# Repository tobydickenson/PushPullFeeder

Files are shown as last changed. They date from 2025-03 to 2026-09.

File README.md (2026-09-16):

# PushPullFeeder

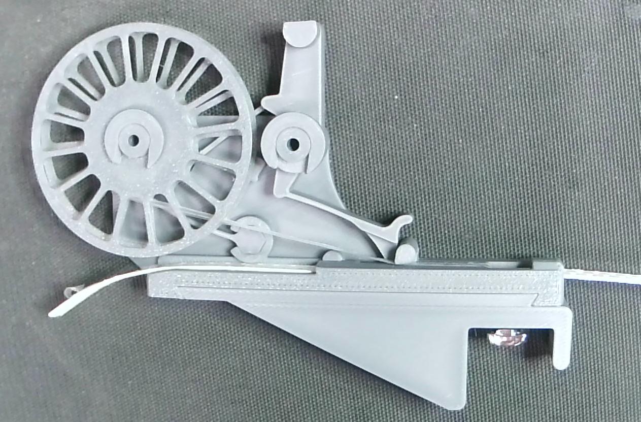
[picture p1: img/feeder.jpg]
A PushPull Feeder


This is a fork of Markmaker’s awesome [PushPullFeeder](https://github.com/markmaker/PushPullFeeder). All of the genius in this design should be credited to Mark, and Mark's [blog](https://makr.zone/?p=399) is a great introduction. Here I present some refinements:

- Some general usability and maintainability improvements.
- A new Bumper Cam mechanism for engaging and disengaging the pushing mechanism with the sprocket hole which greatly improves smoothness.
- Some incremental improvements for feeding parts which were already handled well in Mark’s baseline design.
- Some new features for feeding parts which were outside the scope of Mark’s original design: Parts with deep wide embossed pockets; from 8mm tape with 4mm pockets, up to 24mm with 11mm pockets tested to be working well.
- An alternative machine mounting scheme which is particularly suitable for the lumenpnp machine. This model still supports Mark's mounting scheme too.

The original model supports a dazzling array of configuration parameters. Here I present some useful parameter sets that I use in production on the lumenpnp.

# Changes in Release 176 (March 2026)

- Printability improvements for Bambu printers - My main printer is now A1 mini.
- A huge increase in smoothness. Previous versions push the tape with a pair of sprung teeth. In previous versions a tooth on the pusher dog drags along the top surface of the tape then drops into a sprocket hole before pushing forward. The tape is then pushed over the reverse-blocking tooth, which pops into the sprocket hole at the end of the push. All of these actions cause vibrations and impacts on the tape surface which can cause vibrations which jump 0603 and smaller parts out of pockets. This version uses "the bumper" cam which actively lifts the tooth out of one sprocket hole, and lowers into the next before pushing forward. The reverse-blocking tooth is removed entirely. Having eliminated the main causes of vibrations, it has been possible to eliminate some other vibration-mitigation features which further improves the smoothness of the feed.
- The lever part is much more robust. This is due to some design refinements and some changes to the printing recommendations.
- A compliant spring mechanism to gently support the underside of the tape and hold its top surface at the correct Z position.
- An improved friction clutch for film peeling.
- Further improvement to prevent the tape getting jammed. A jammed tape can cause the lever to break when activated.
- Improved rigidity on the machine mount.
- Some changes to recommended printer settings - see below.
- Change to assist in assembling the film peeling spool onto the base.

## Changes since the first alpha release of this branch

- Increased peeling force.
- Changes to the compliant spring and base to accomodate super-thin and super-fat tapes.
- Move the paper tape pick window for better alignment with 0402 parts.
- Fix a chamfer on the lever axle hole.
- Change some through holes to blind holes for a cleaner faster bottom surface print.

# Changes in Release 74 (August 2025) excluding those later reverted in Release 176

## Improvements for parts in paper tape
- The "inset" is the part which holds the tape as it passes through the feeder. There are several changes to the profile of the inset to reduce part jumpiness.
- The grip after the pick window is arched to allow any mispicked parts to be expelled out the front of the feeder.
- A gentle lead-in to help insert the tape into the back of the inset.

## Improvements for parts in embossed plastic tape
- An option to print the inset in two halves. The left half supports under the sprocket holes on the left side of the tap. The right half supports under the right side of the tape, and grips the tape from above. This avoids any geometry limitations due to 3d printer overhang angle, and allows insets for tapes with deep and wide embossed pockets.

## Improvements for cover film peeling
- The film peeling edge has been remodelled to ensure it is perpendicular to the tape feed direction, which reduces the risk of the film tearing.
- A narrower mount for the peeling spring gives a clearer path for film onto the peeling spool.
- With wider tapes, the friction wheel sometimes had a problem where there is an excess of friction due to a large contact area, and the peeling force is too large. The film can pull the tape ahead of the sprocket hole engagement. A tapered friction wheel controls the contact area used with wider tapes.
- “The scraper” is a new optional feature which can be used for feeding parts that tend to stick to the film rather than stay in their pocket. This is a finger which holds the parts in their pocket until they advace to the pick location.

## Changes to the lever
- Mark's original design horizontally scaled the lever and various other design features in proportion to the tape width. That scheme has been changed to have a fixed width lever. I think this makes more sense; tapes of all widths are advanced using sprocket holes of the same dimensions. Furthermore this reduces the number of different parts that need to printed.
- There are some geometry changes to give more space around any part that might be carried by the other nozzle on a dual-nozzle machine. Firstly, the angle of the lever arm has been changed to be exactly vertical. This increases the X/Y space available for the part on the other nozzle.
- Secondly, the knob at the top of the lever arm has a flatter profile. This increases the Z space available for the part on the other nozzle.

## Usability and printability improvements
- Added some fillets in places which previously saw some brittle fractures.
- Sometimes the inset can be a tight fit on the base, so some features have been added to aid disassembly. Finger grips for pulling it off, and a second hole through the base for pushing it off.
- Improved retention of the film peeler spool washer, or reel-holder arm counterpart.

## A new optional machine mount.
Use with the lumenpnp has several design requirements that are quite different to Mark’s baseline design.

- The lumenpnp head has a large Y offset between nozzles and camera which makes it impractical to use the camera with the PushPull feeder. Since we can’t use the camera to fine-tune the pick location, we benefit from the pick location being very stable and repeatable. The feeder is therefore mounted onto a 20mm extrusion directly underneath the pick location. This new 20mm extrusion is mounted to the machine side rails using 2 angle brackets at each end for rigidity. See photos below.
- The feeder is mounted onto the extrusion using a 6mm M3 countersunk screw and t-nut, directly underneath the pick location. The screw is captive in the feeder once the inset is fitted, and the screw can be driven through a hole in the base of the inset so that it can be fitted and removed while tape is loaded on the feeder; you just need to cut off the empty tape end, and retract the tape a little to expose the hole.
- There is a separate git repository for a [lumenpnp z gantry](https://github.com/tobydickenson/PushPullGantry) modification which includes the hook needed for pushing and pulling the feeder lever.

## Extra-deep feeders
- This includes a configuration for a feeder for parts up to 11mm tall in 16mm or 24mm tape. This feeder has a deeper base and deeper inset to support the deep tape.
- A correspondingly shorter lever is used to maintain a safe-z height consistent with the normal feeders. This needs a slightly slower push/pull speed.

# How to print

STL files for immediate printing are in the `printme` directory.

All parts should be printed in PETG. PETG has a stable modulus over temperature, which is required for the spring parts. PETG has good abrasion resistance, which is required for the lever and base which interact at "the bumper".

All models are tested on a Bambu printer with 0.4mm nozzle. All parts print with the standard "0.12mm High Quality" print profile, with the exception of the Lever part (see below)

For other slicers, use a "layer start: sharpest corner" or "seam: aligned" option. Plain bearing surfaces have a helical groove which is designed to capture the layer start, ensuring that the exposed bearing surface is a smooth continous extrusion.

IMPORTANT: Before printing, it is critical that your printer can produce dimensionally accurate parts. Print the `printme/nuts/nuts-xxx.stl` file, and perform the following checks:

- Check the bottom surface (first layer) is smooth and correct. A textured build plate is ok.
- Check the top surface is smooth and correct. It is ok to have some under-extrusion visible in the top surface, and indeed this is better than a precise flow calibration which shows a smooth top surface but makes surface dimensions more sensitive to any variation in flow.
- Check the parts are circular, not elliptical.
- Check the parts are circular, not a lower polygon count approximation substituted by your slicer.
- Check the outer diameter of the male part is 8.00mm, and its surface is smooth. This is a dimension accuracy check.
- Check the inner diameter of the female part printed with "10" is 8.10mm. This is labelled 10 because of the 10x10µm size increase. Fitting the male part inside this hole is a validation check of axle plain bearings. The axle should turn smoothly, without being loose. See the assembly video (linked below) for how this axle should appear.
- Check the inner diameter of the other female part printed with "0" is 8.00mm. Fitting the male part inside this hole is a validation of interference fit assembly.

Any problems need to be addressed first, through either printer hardware maintenance or slicer configuration. The printed feeder is very sensitive to dimensional tolerance; if your printer can't produce an accurate nut then it will not be able to print a working feeder!

If any of the diameters are wrong then you will need to adjust a "X-Y hole compensation" slicer option with a correction offset. Re-print the test nuts and re-check.

The **Lever** parts has a leaf spring feature which needs a modified slicer profile. The important constraint is that the leaf springs must be printed as continuous extrusions; any discontinuities will result in a stress concentration which will make the spring insufficiently robust. On a Bambu printer with 0.4mm nozzle this can be acheived by setting the "Outer wall" and "Inner wall" options to **0.3mm**. Please confirm this has the desired effect using your slicer preview. The leaf springs should be printed as four wall extrusions with no discontinuities, as highlighted in green below. The red highlights show various discontinuities which would cause the leaf spring to be insufficiently robust (although they will still probably feed several thousand parts before breaking with fatigue, so dont panic if this is difficult to get right on your first print).

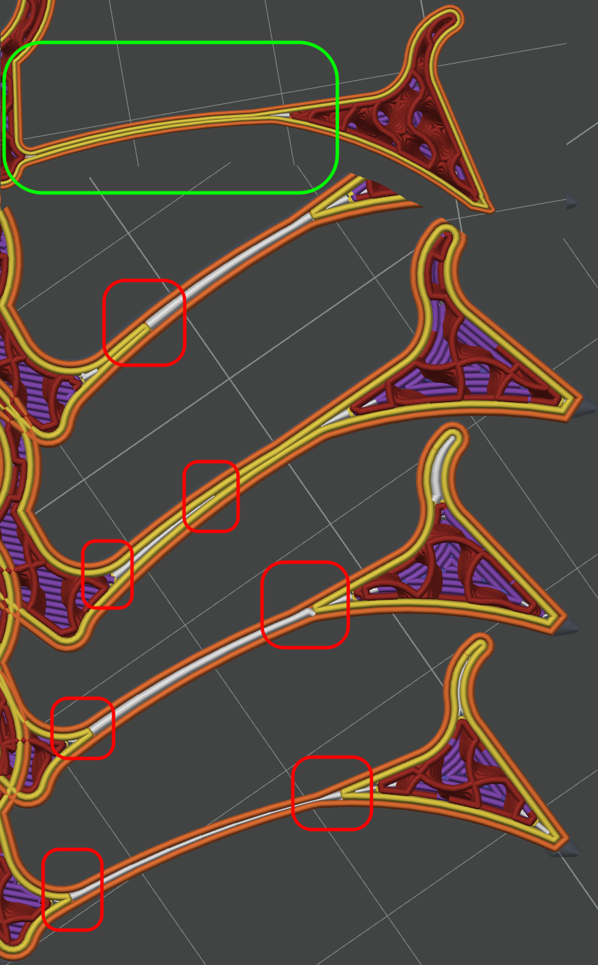
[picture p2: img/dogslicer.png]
Lever slicing


# Recommended movement steps

The movement steps described below are a little different to those described in Mark’s setup video. The key difference is that the start location is in front of the feeder, not above. This means that the programmed push/pull motion takes the hook actuator well away from the feeder, and therefore the push/pull mechanism does not need to be considered when configuring safe-z.

Manually move the feeder’s push/lull lever back to its home position, with the “dog” pusher fully forward against the end stop.

- Set the **Start** location with the tip of the the hook 1mm above the lever, and 10mm in front.
- **Mid1** location should be set with the hook 1mm above the lever, and aligned ready to move down. Note that the “heel” of the hook ensures that the lever is returned back into its home position during the movement to this location.
- **Mid2** location: The hook moves down 3mm and forward 0.5mm. This engages the hook onto the lever.
- **Mid3** location: This is the position with the hook under tension pulling back, pushing the tape forward. Set this position to the same Z as Mid2, and 1.5mm back. You may need to adjust the 1.5mm offset; it needs to push the tape all the way forwards (for repeatable positioning) without unduly bending the lever arm. Set 20ms pause time to ensure the actuator remains momentarily stationary at this end point.
- **End** location: This is the position with the hook under tension pushing forward. Relative to Mid 2 this is 10mm forward and 2.5mm down. 10mm is a good starting point, but you might find this needs to be increased up to around 12mm, depending on machine rigidity. Set 20ms pause time to allow the dog to drop of the top of the bumper cam.

The tickboxes control which locations are visited for the forward and backward stroke, and which locations are repeated when pumping multiple cycles in one visit. As shown below, Mid3 is skipped on the forward cycle, Mid 2 skipped on the backwards cycle, and only Mid3 and End are repeated for multiple cycles.

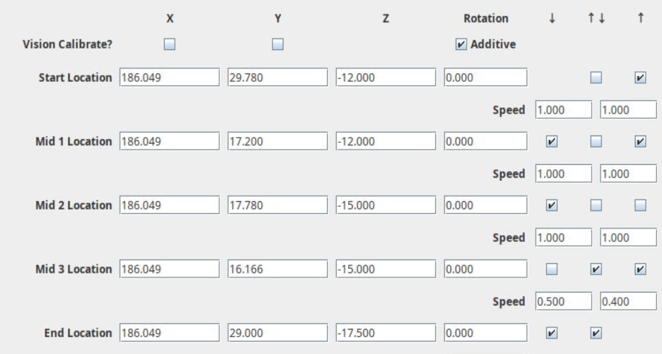
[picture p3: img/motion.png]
Motion Steps


# OpenSCAD versions

At the time of writing this, the openscad nightly build has some huge improvements and the "released" version is now getting quite old. This model is primarily developed using a nightly build. It probably does work with the released version of openscad too but this is untested.

If any openscad maintainers are reading this; the improvements are very much appreciated and I would love to see a stable release sometime soon.

# BOM

Feeder options are:
 * Tape width.
 * For 8mm tape, paper and plastic tape have different insets.
 * The thickest 8mm paper tape need a compliant spring with a larger gap.
 * For 8mm and 12mm feeders there is a on option to include the "scraper".
 * The 24mm feeder supports deeper pockets. There is an option to convert a 24mm extra-deep feeder for 16mm tape.

STL files are in the `printme` folder for direct printing.

| | | | | | | | | | | |
| --- | --- | --- | --- | --- | --- | ---- | ---- | ---- | ---- | ---- |
| **Options** | | | | | | | | | | |
| Tape width (mm) | 8 | 8 | 8 | 8 | 8 | 12 | 12 | 16 | 16 | 24 |
| Paper tape? | yes | fat | | yes | | | | | | |
| Plastic tape? | | | yes | | yes | yes  | yes  | yes  | yes  | yes  |
| Max embossed pocket depth (mm) | | | 3 | | 3 | 3 | 3 | 3 | 11 | 11 |
| Has a scraper? | | | | yes | yes | | yes  | | | |
| | | | | | | | | | | |
| **Printed Parts** | | | | | | | | | | |
| base-8mm | 1 | 1 | 1 | 1 | 1 | | | | | |
| base-12mm | | | | | | 1 | 1 | | | |
| base-16mm | | | | | | | | 1 | | |
| base-24mm-extra-deep | | | | | | | | | 1 | 1 |
| | | | | | | | | | | |
| inset-8mm-left | 1 | | | 1 | | | | | | |
| inset-8mm-left-fat | | 1 | | 1 | | | | | | |
| inset-8mm-right | 1 | 1 | | | | | | | | |
| inset-8mm-right-scraper | | | | 1 | | | | | | |
| inset-8mm-12mm-16mm-plastic-left | | | 1 | | 1 | 1 | 1 | 1 | | |
| inset-8mm-plastic-right | | | 1 | | | | | | | |
| inset-8mm-plastic-right-scraper | | | 1 | | 1 | | | | | |
| inset-12mm-plastic-right | | | | | | 1 | | | | |
| inset-12mm-plastic-right-scraper | | | | | | | 1 | | | |
| inset-16mm-plastic-right | | | | | | | | 1 | | |
| inset-24mm-extra-deep-left | | | | | | | | | 1 | 1 |
| inset-16mm-extra-deep-right | | | | | | | | | 1 | |
| inset-24mm-extra-deep-right | | | | | | | | | | 1 |
| | | | | | | | | | | |
| lever-8mm-12mm-16mm | 1 | 1 | 1 | 1 | 1 | 1 | 1 | 1 | | |
| lever-extra-deep | | | | | | | | | 1 | 1 |
| | | | | | | | | | | |
| scraper-8mm | | | | 1 | 1 | | | | | |
| scraper-12mm | | | | | | | 1 | | | |
| | | | | | | | | | | |
| friction-8mm | 1 | 1 | 1 | 1 | 1 | | | | | |
| friction-12mm | | | | | | 1 | 1 | | | |
| friction-16mm | | | | | | | | 1 | 1 | |
| friction-24mm | | | | | | | | | | 1 |
| spool-left | 1 | 1 | 1 | 1 | 1 | 1 | 1 | 1 | 1 | 1 |
| spool-right-8mm | 1 | 1 | 1 | 1 | 1 | | | | | |
| spool-right-12mm | | | | | | 1 | 1 | | | |
| spool-right-16mm | | | | | | | | 1 | 1 | |
| spool-right-24mm | | | | | | | | | | 1 |
| | | | | | | | | | | |
| drum-8mm | 1 | 1 | 1 | 1 | 1 | | | | | |
| drum-12mm | | | | | | 1 | 1 | | | |
| drum-16mm | | | | | | | | 1 | 1 | |
| drum-24mm | | | | | | | | | | 1 |
| washer | 2 | 2 | 2 | 2 | 2 | 2 | 2 | 2 | 2 | 2 |
| blocking-spring | 1 | 1 | 1 | 1 | 1 | 1 | 1 | 1 | 1 | 1 |
| | | | | | | | | | | |
| **Hardware** | | | | | | | | | | |
| 6mm M3 countersunk screw | 1 | 1 | 1 | 1 | 1 | 1 | 1 | 1 | 1 | 1 |
| M3 t-nut | 1 | 1 | 1 | 1 | 1 | 1 | 1 | 1 | 1 | 1 |

# Photos!

NB some of these photos show release 74.

## 8mm Feeder Photo

Some 8mm feeders mounted on the machine. One has a scraper.

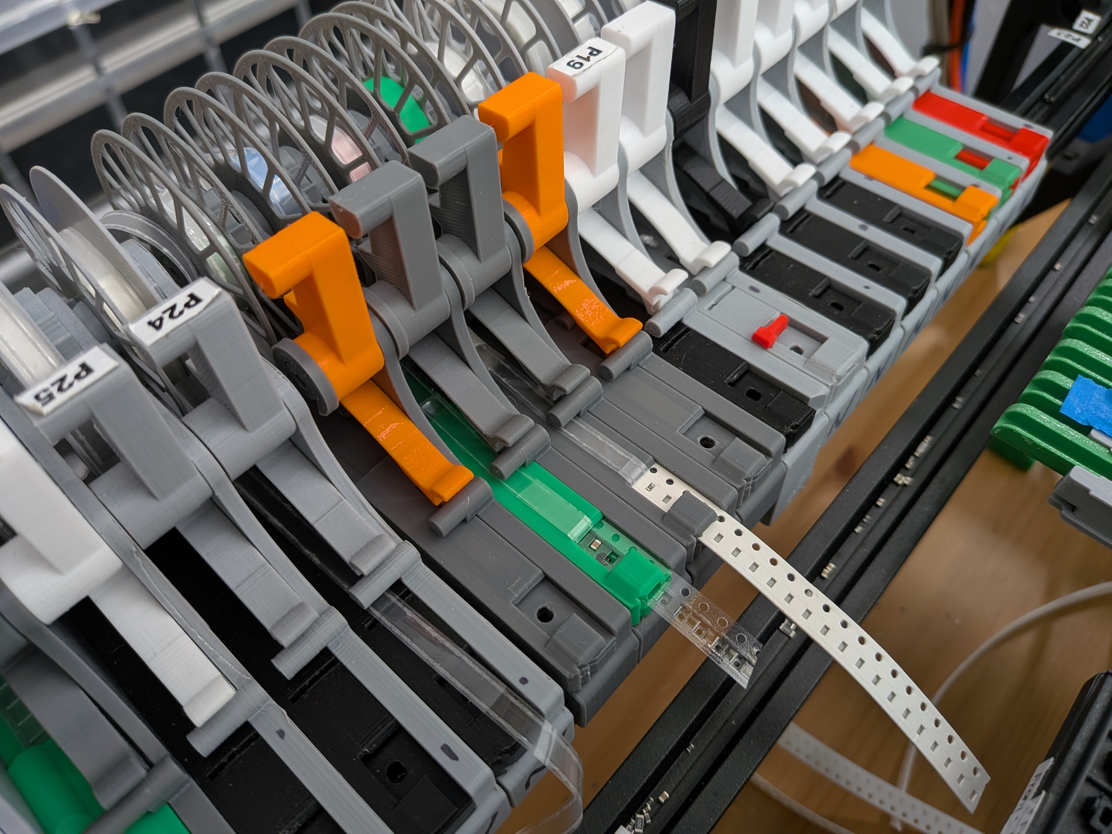
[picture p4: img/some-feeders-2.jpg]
Some PushPull Feeders


## 24mm Feeder Photo

A 24mm feeder with extra-deep pockets, and several 12mm feeders. Note the extra-deep feeder has an extra-short lever to keep a consistent hook engagement height.

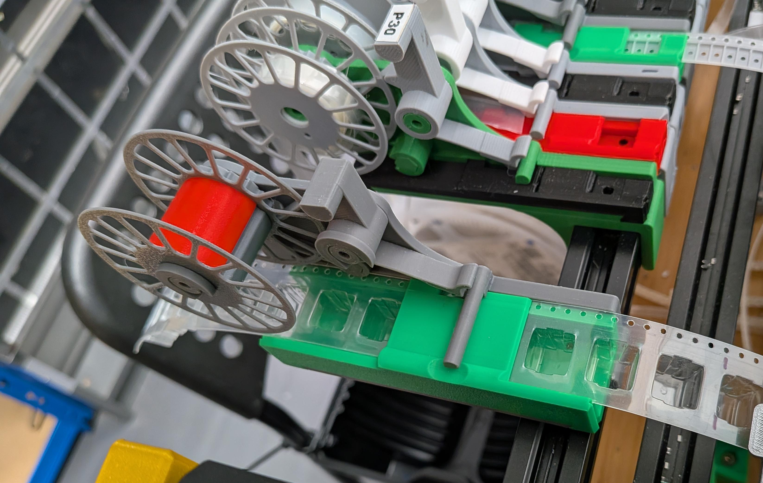
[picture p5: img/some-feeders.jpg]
Some PushPull Feeders


## Extrusion Photo

This shows the feeders mounted onto the 20mm extrusion, and that extrusion mounted onto the side rails of the lumenpnp machine.

This is my preferred location on a lumenpnp; it puts the feeder right at the front of the machine. The hook can only just reach the lever, and the nozzles only just reach the parts at the pick location, so there is minimal waste of build area on the rest of the machine.

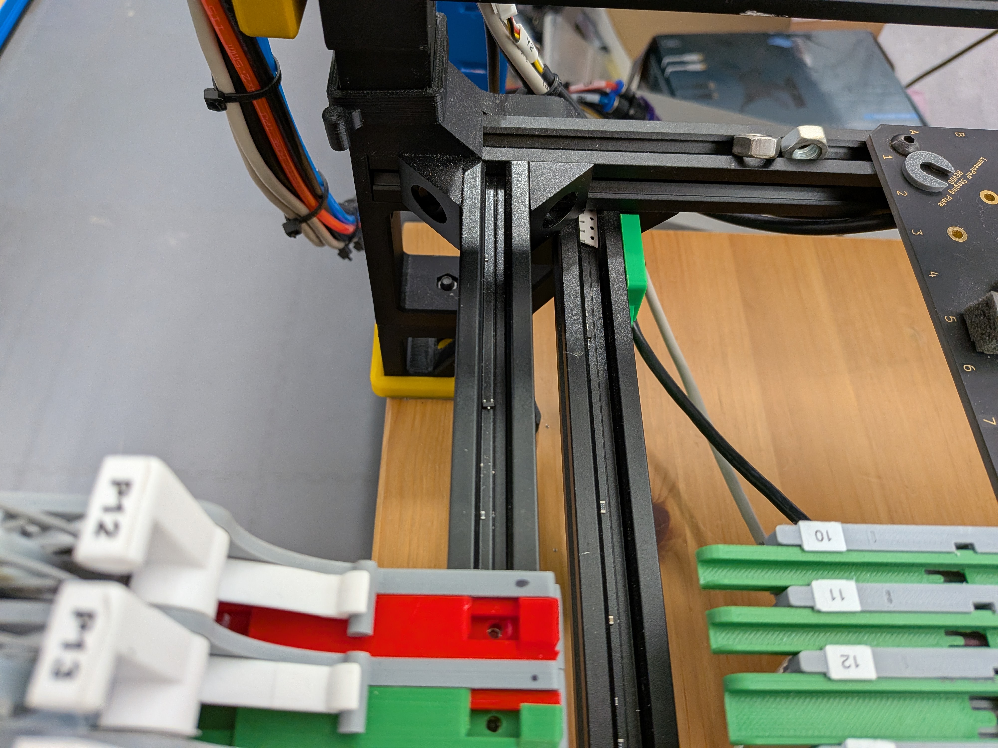
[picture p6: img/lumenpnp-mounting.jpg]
Mounted on the lumenpnp


Alternatively the feeders extrusion could be stacked on top of the front rail. An advantage of this approach is that the feeder extrusion does not have to be the full width of the machine. (Please share if you have a photo of such a setup)

## Spool Photo

This is a 24mm spool. The red drum is to clamp the film.

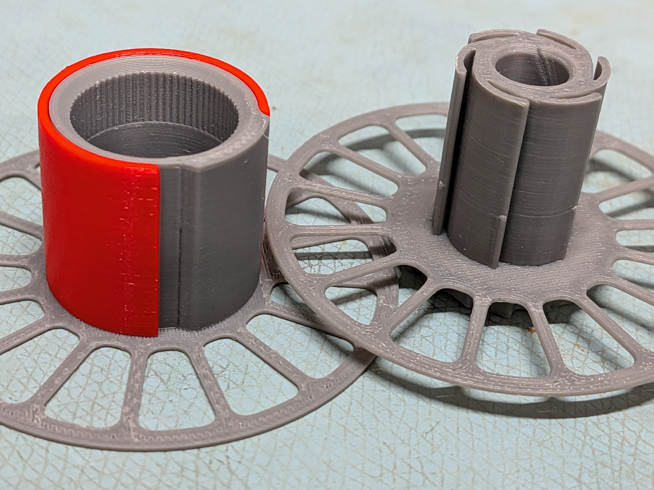
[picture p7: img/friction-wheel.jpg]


## Scraper Photo

The scraper finger removed from the inset. (The feeders in this photo are the previous version, release 74)

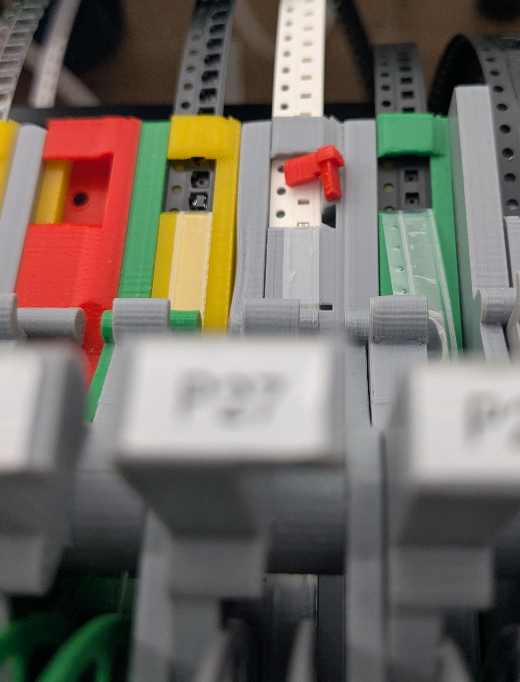
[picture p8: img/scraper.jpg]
Scraper


## Paper Inset Photo

The inset for paper tape is printed in two parts. The left part (green) is a compliant sprung platform that supports the full width of the tape, holds it at the right Z position, and accomodates tapes of different thicknesses.

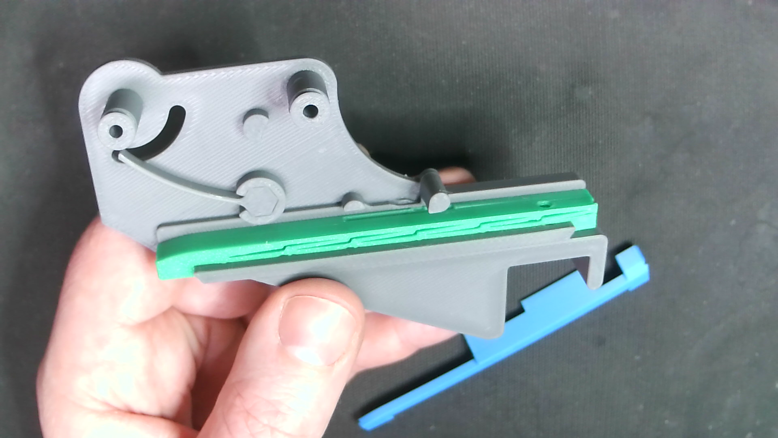
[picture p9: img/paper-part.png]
Part-assembled feeder for paper tape


The right part (blue) of the inset for paper tape is the cover which defines the tape upper surface Z position. Here the feeder is fully assembled.

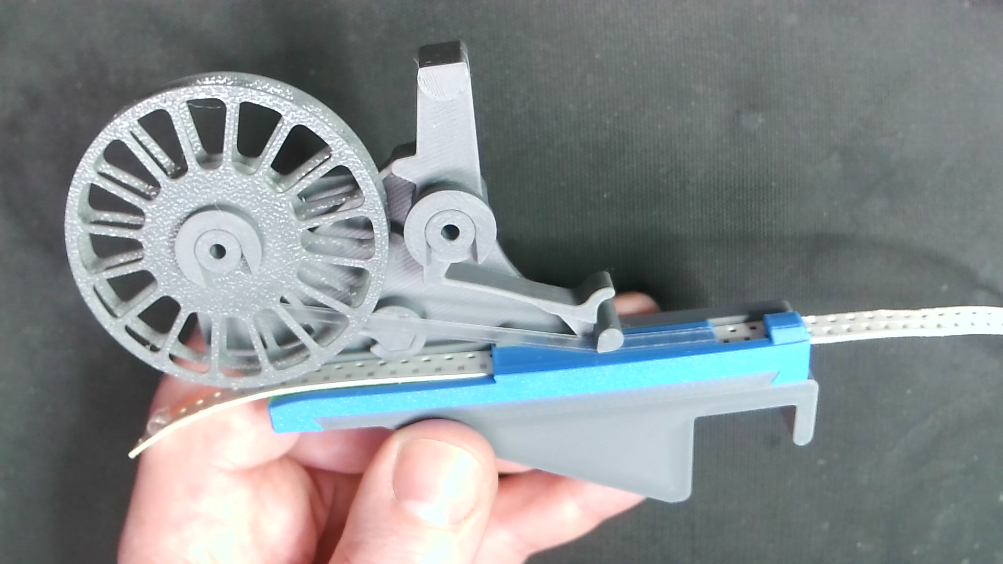
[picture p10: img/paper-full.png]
Fully assembled feeder for paper tape


## Plastic Inset Photo

The inset for plastic tape with embossed pockets is also printed in two parts. The left part (green) is a compliant sprung platform that supports just the sprocket hole edge.

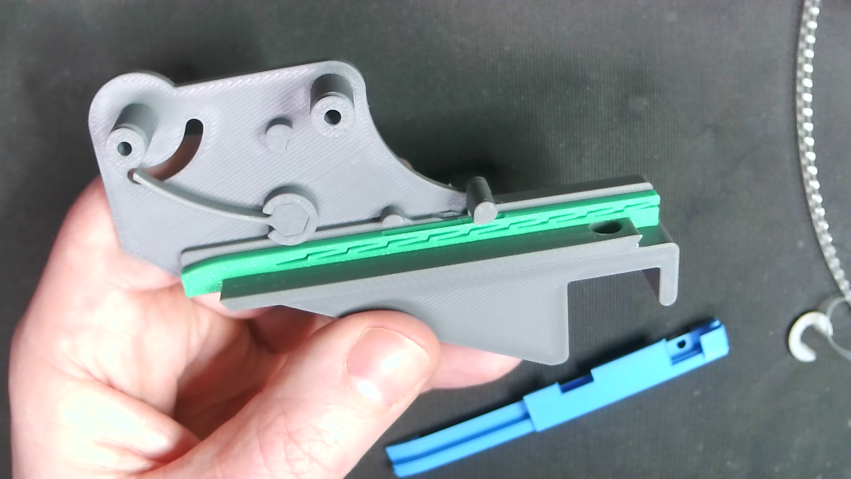
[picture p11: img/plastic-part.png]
Part-assembled feeder for plastic tape


The right part (blue) hold the right edge of plastic tape. Here the feeder is fully assembled.

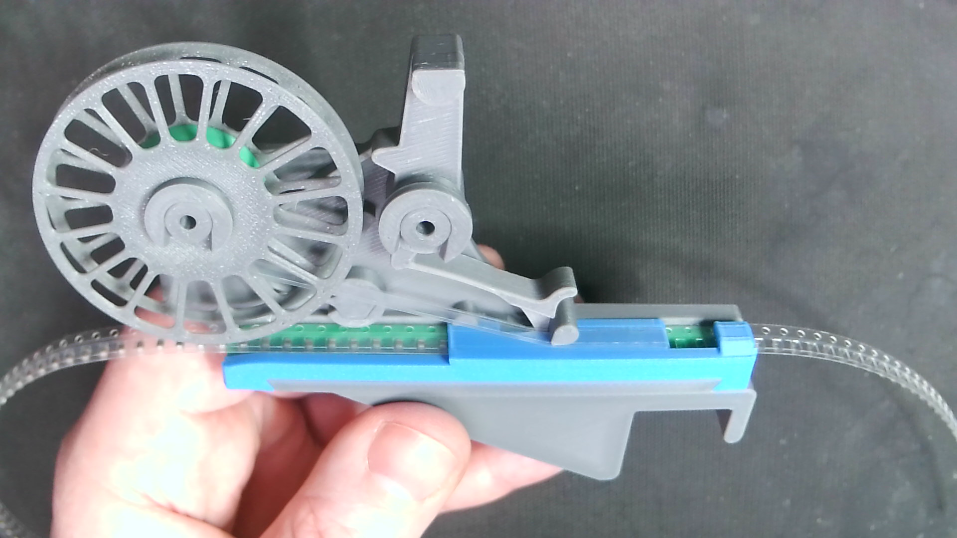
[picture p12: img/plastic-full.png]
Fully assembled feeder for plastic tape


## Bumper Cam Photo

This shows the action of the bumper cam. It actively lifts the pusher tooth out of one sprocket hole, and lowers into the next before pushing forward.

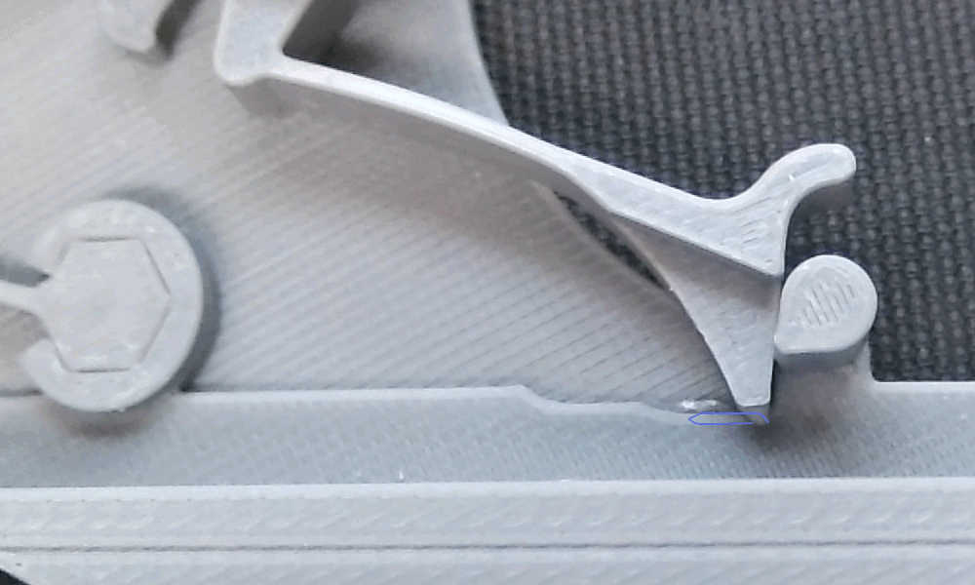
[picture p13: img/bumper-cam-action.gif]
The bumper cam action


This is the profile of the bumper cam. When the pusher dog moves backward, it rides over the top of the cam (blue path)
which quickly withdraws the pusher thorn from the tape hole to avoid having it drag along the top surface of the tape.
When it pushes forward it rides to the right of the cam (green path) which lowers the pusher thorn into the hole
before pushing forward.

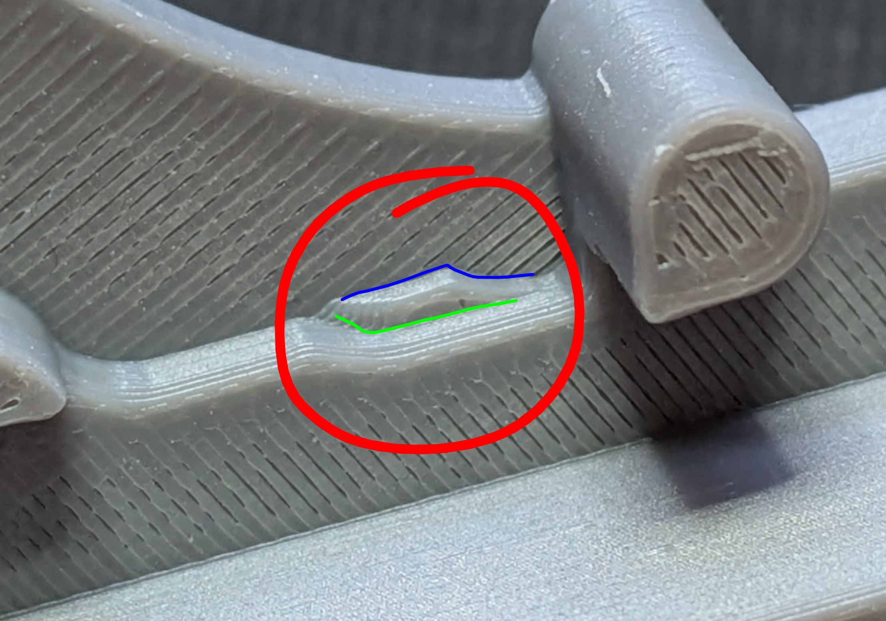
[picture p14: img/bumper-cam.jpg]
The bumper cam profile


# Videos

The feeder in use, feeding and placing four parts. The feeders in this video are the previous version, release 74.

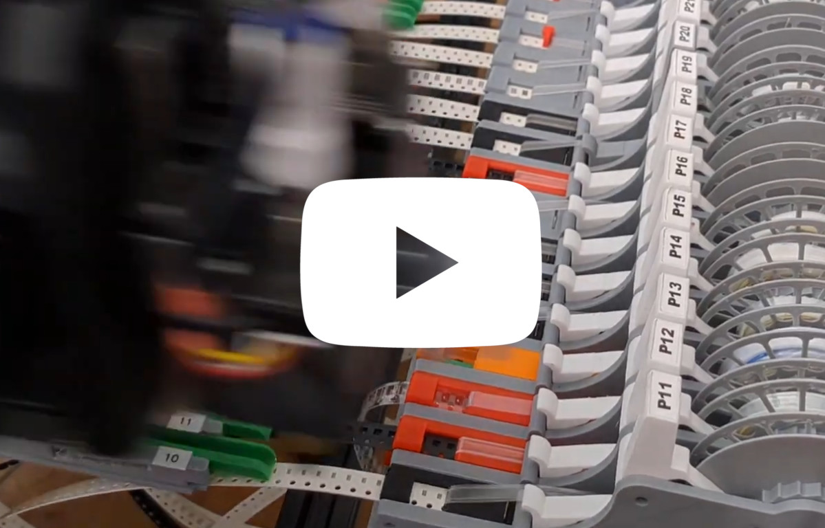
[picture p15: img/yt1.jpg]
The feeder in use, feeding and placing four parts (https://www.youtube.com/watch?v=HmRUPP_7lOk)


A single feed cycle, at 10% speed

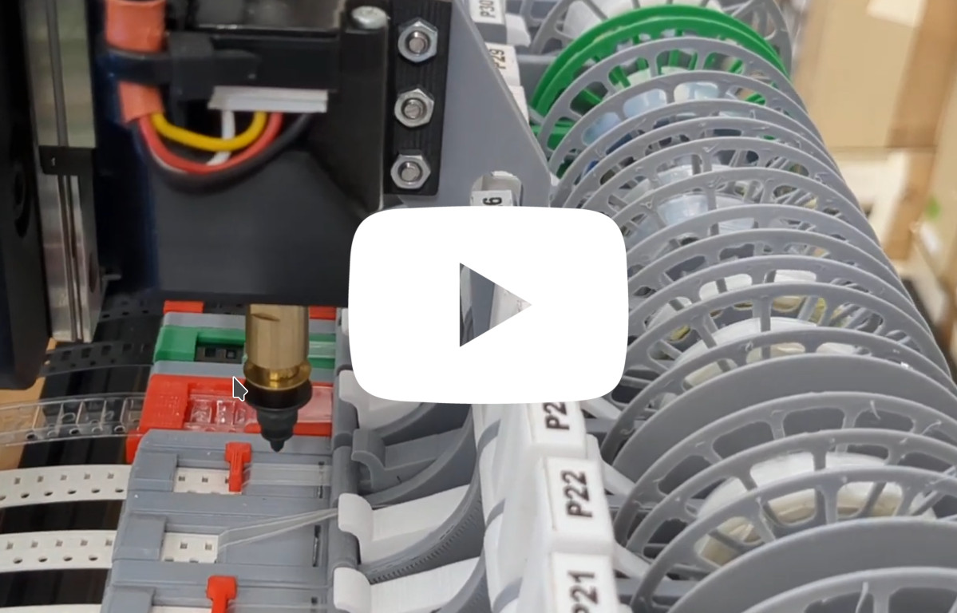
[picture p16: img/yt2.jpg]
A single feed cycle, at 10% speed (https://www.youtube.com/watch?v=0Pb1ezohiMo)


Assembly instructions

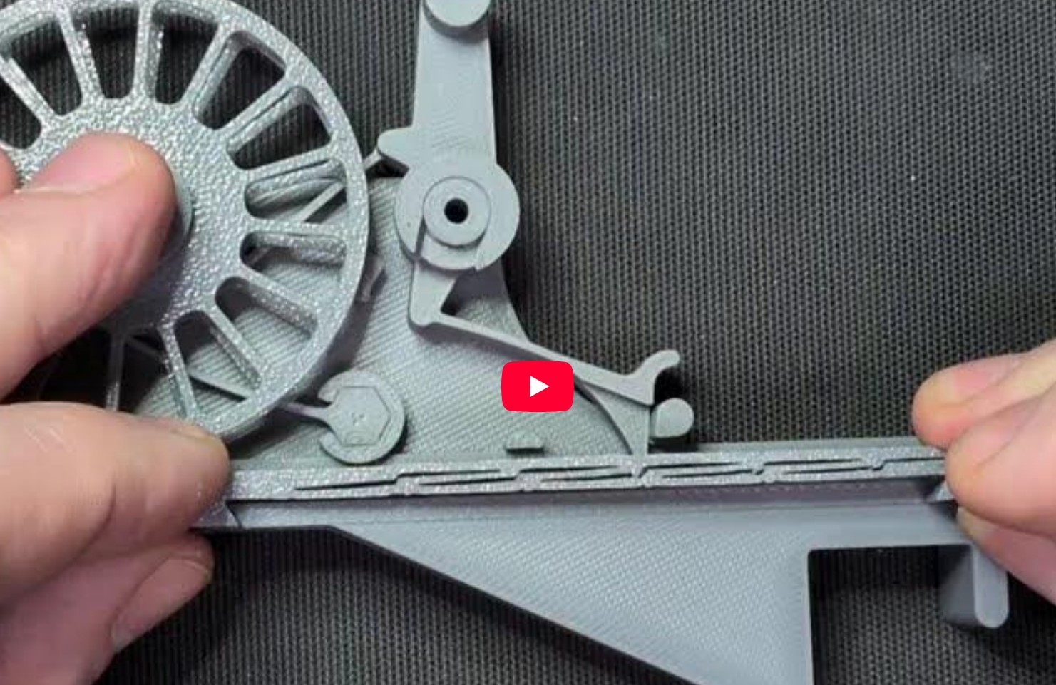
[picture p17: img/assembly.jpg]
Assembly instructions (https://www.youtube.com/watch?v=XDT4DxTVX4w)


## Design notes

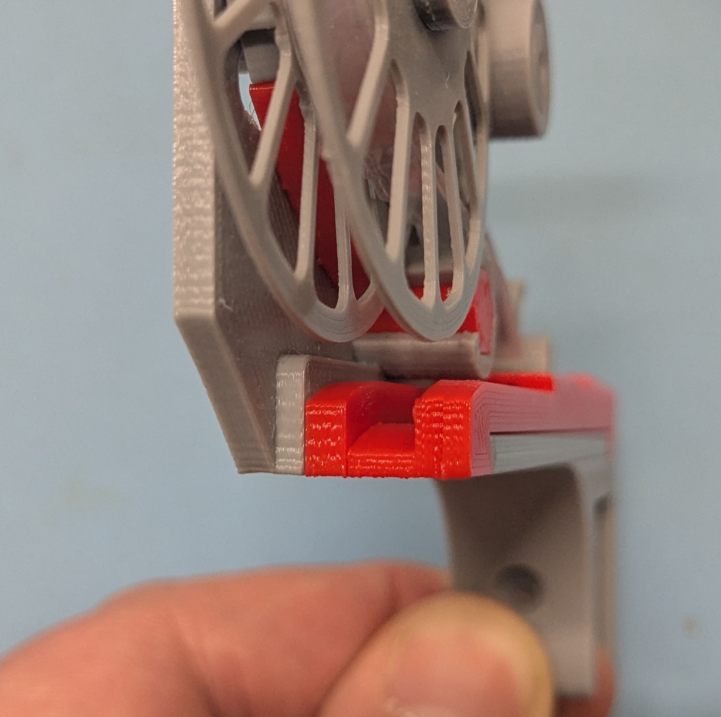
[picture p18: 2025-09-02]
img/two-part.jpg

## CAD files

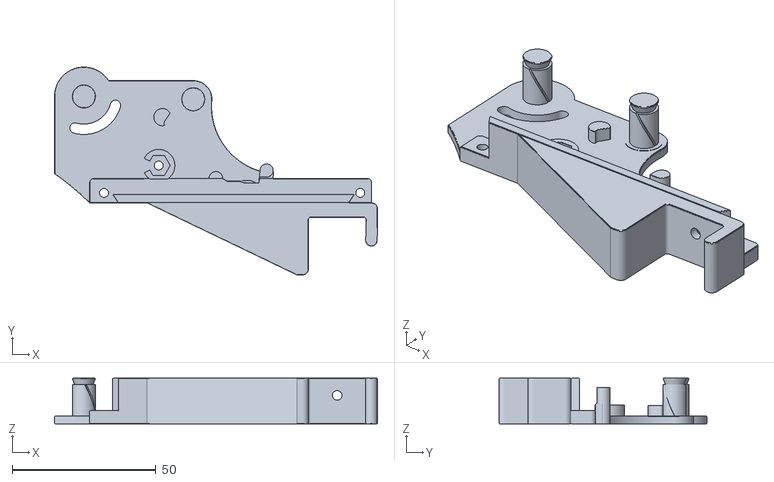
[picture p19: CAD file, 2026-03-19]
printme/base/base-8mm-172.stl
112.2 x 72.2 x 15.9

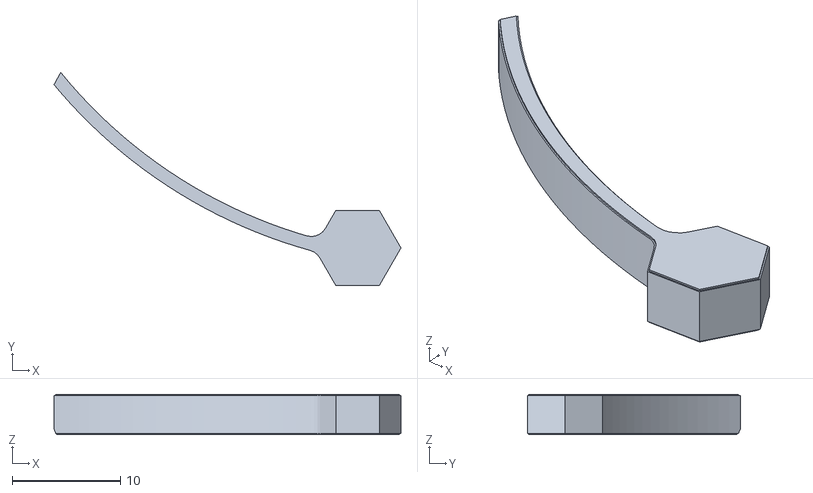
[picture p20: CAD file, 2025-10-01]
printme/block-spring/blocking-spring-87.stl
32.0 x 19.7 x 3.70

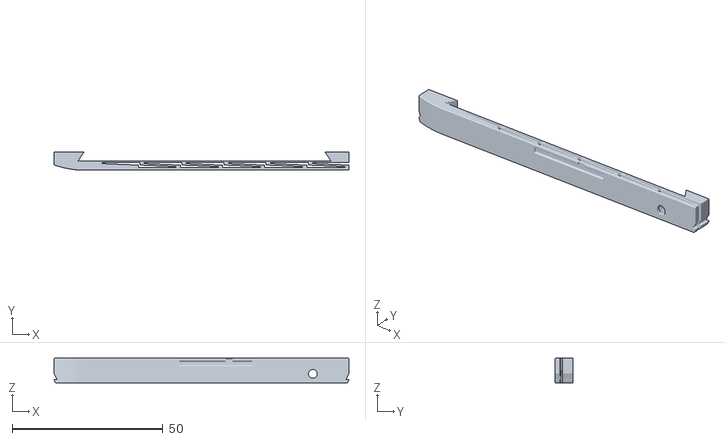
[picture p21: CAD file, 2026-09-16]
printme/inset-paper/left/inset-8mm-left-fat-190.stl
98.0 x 6.12 x 8.15

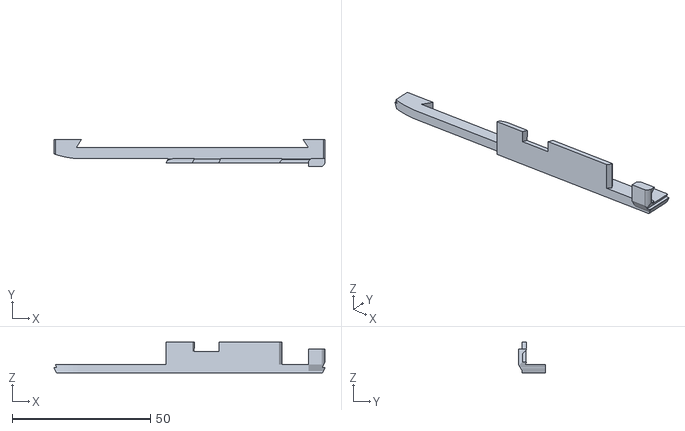
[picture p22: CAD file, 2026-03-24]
printme/inset-paper/right/inset-8mm-right-174.stl
98.0 x 9.92 x 11.1

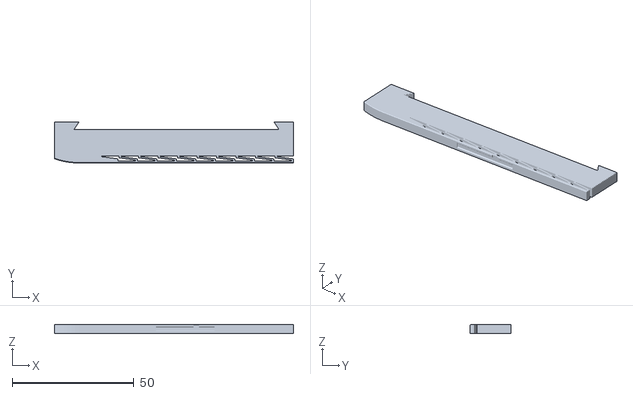
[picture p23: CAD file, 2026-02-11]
printme/inset-plastic-extra-deep/left/inset-24mm-extra-deep-left-143.stl
98.0 x 16.8 x 3.53

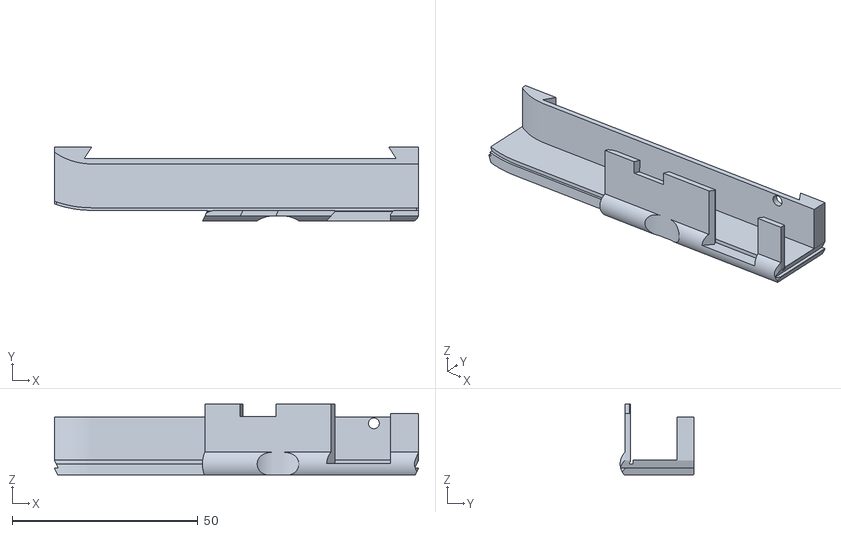
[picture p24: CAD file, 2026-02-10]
printme/inset-plastic-extra-deep/right/inset-16mm-extra-deep-right-141.stl
98.0 x 19.8 x 19.1

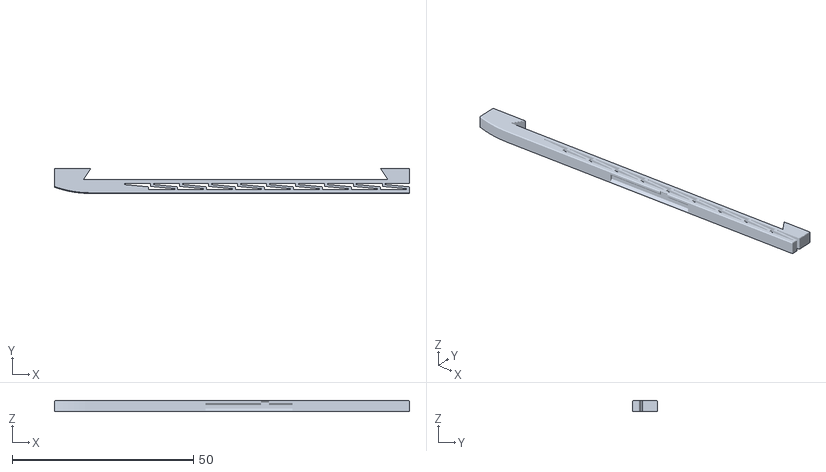
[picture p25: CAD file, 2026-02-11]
printme/inset-plastic-normal-depth/left/inset-8mm-12mm-16mm-plastic-left-143.stl
98.0 x 6.92 x 3.03

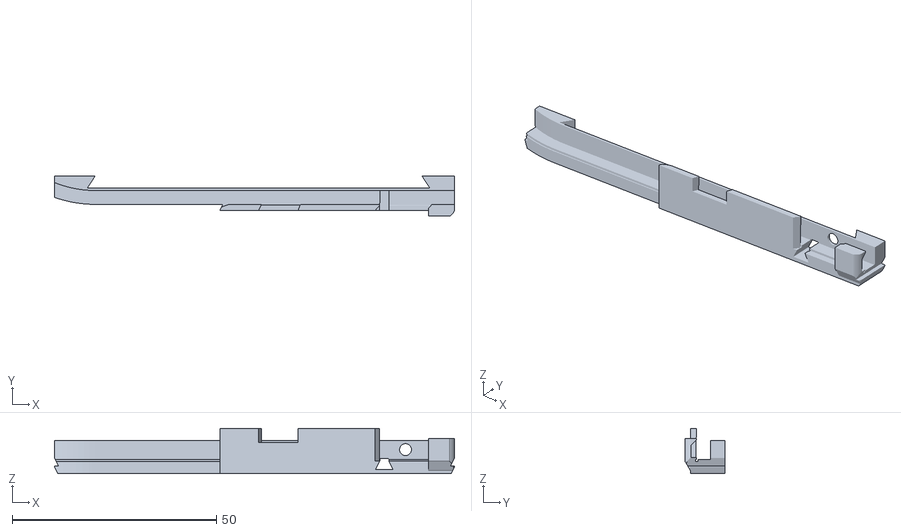
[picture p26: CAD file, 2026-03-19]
printme/inset-plastic-normal-depth/right/inset-8mm-plastic-right-scraper-171.stl
98.0 x 9.92 x 11.1

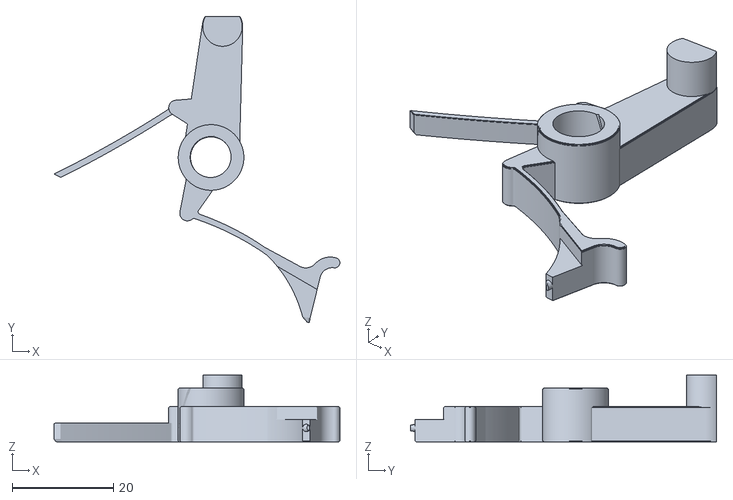
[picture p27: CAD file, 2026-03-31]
printme/lever/lever-8mm-12mm-16mm-176.stl
56.6 x 60.6 x 13.2

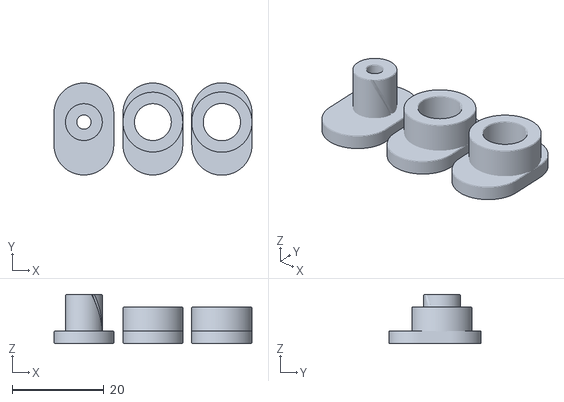
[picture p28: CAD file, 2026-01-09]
printme/nuts/nuts-zero-126.stl
43.1 x 20.1 x 10.7

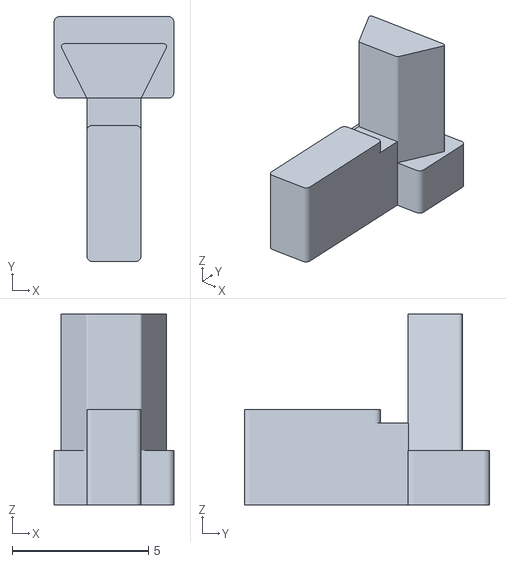
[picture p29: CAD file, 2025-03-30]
printme/scraper/scraper-8mm-62.stl
4.40 x 9.00 x 7.00

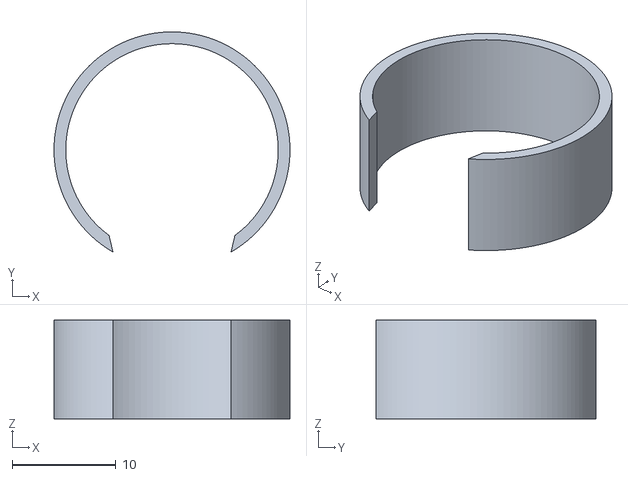
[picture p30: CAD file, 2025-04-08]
printme/spool-drum/drum-12mm.stl
22.8 x 21.3 x 9.52

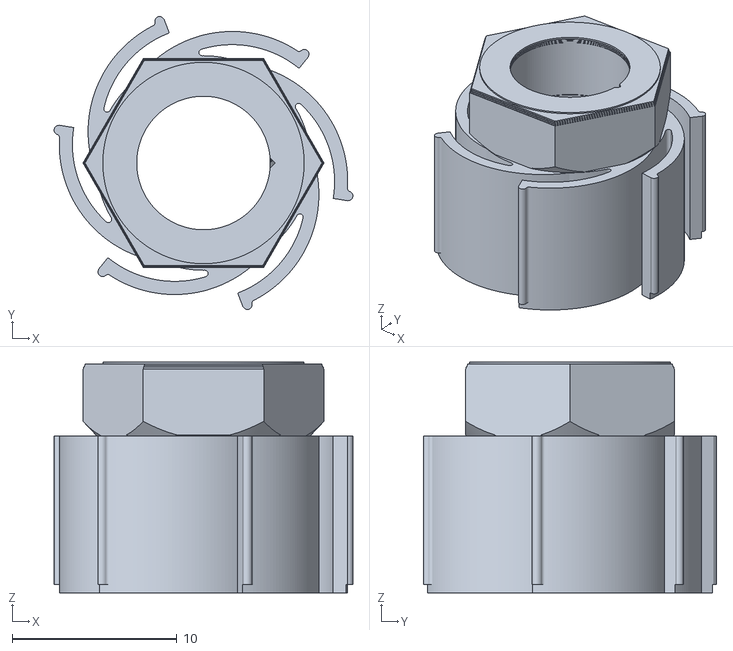
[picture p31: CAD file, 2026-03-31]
printme/spool-friction-wheel/friction-12mm-176.stl
18.1 x 17.8 x 14.0

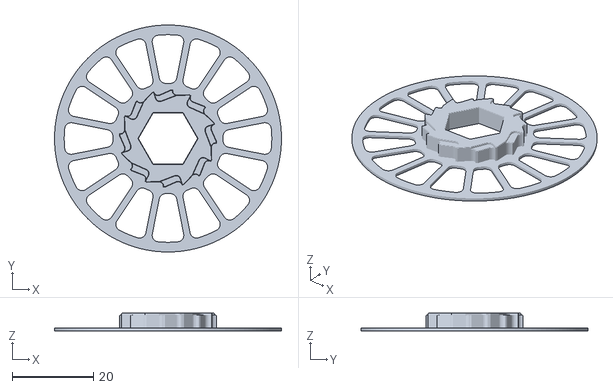
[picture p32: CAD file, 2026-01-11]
printme/spool-left/spool-left-126.stl
56.0 x 56.0 x 4.40

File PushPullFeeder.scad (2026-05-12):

/*
 * Copyright (C) 2020 <mark@makr.zone>
 *
 * Inspired by Dining-Philosopher's Litefeeder
 * https://github.com/dining-philosopher/litefeeder
 * and Jed Smith's Litefeeder++ friction wheel
 * https://loonatec.com/pnp-semi-automatic-feeder/
 * 
 * The PushPullFeeder is free software: you can redistribute it and/or modify it under the terms of the GNU
 * General Public License as published by the Free Software Foundation, either version 3 of the
 * License, or (at your option) any later version.
 * 
 * The PushPullFeeder is distributed in the hope that it will be useful, but WITHOUT ANY WARRANTY; without even
 * the implied warranty of MERCHANTABILITY or FITNESS FOR A PARTICULAR PURPOSE. See the GNU General
 * Public License for more details.
 * 
 * You should have received a copy of the GNU General Public License along with OpenPnP. If not, see
 * <http://www.gnu.org/licenses/>.
 * 
 * For more information visit https://makr.zone/tag/feeder/
 */



/* [ Make Options ] */

// Single/special selection
option=0; // [0:"* Individual switches (see below...)", -1:"* Phase I Parts", -2:"* Phase II Parts", -3:"* Everything", -4:"* Ratchet parts", 1:"Base plate", 2:"Lever", 3:"Spool, base", 4:"Spool, cover", 5:"Friction wheel", 6:"Tape inset", 7:"Ratchet blocking spring", 8:"Reel counterpart", 9:"Handle and lock", 10:"Liteplacer nozzle adapter", 11:"Liteplacer lever actuator", 12:"Spent Tape Chute", 13:"Test print"]

// Base plate of the feeder 
make_base_plate         = true;
// Lever with the dog
make_lever              = true;
// Spool left side (base), with ratchet wheel
make_spool_left        = true;
// Spool right side (cover)
make_spool_right       = true;
// Friction wheel, connecting the two spool halves with a slip-transmission
make_friction_wheel     = true;
// Exchangable tape inset, allows to use different tape thickness/embossing
make_inset              = true;
//
make_scraper            = true;
// Spring blocking the ratchet from going in reverse
make_blocking_spring    = true;
// Reel holder counterpart holding the reel up on the other side (for narrow reels only)
make_reel_counterpart   = true;
// Handle and lock for the extrusion mount
make_handle_lock        = true;
// Liteplacer specific nozzle adapter
make_nozzle_adapter     = false;
// Liteplacer specific lever actuator
make_lever_actuator     = false;
// Simple spent tape chute
make_tape_chute         = false;
// Test print
make_test_print         = false;

phase1 = (option == -1);
phase2 = (option == -2);
everything = (option == -3);
ratchet_parts = (option == -4);

do_base_plate         = (option == 0 && make_base_plate)         || (option ==  1)  || everything || phase1 || ratchet_parts;
do_lever              = (option == 0 && make_lever)              || (option ==  2)  || everything || phase2 || ratchet_parts;
do_spool_left         = (option == 0 && make_spool_left)         || (option ==  3)  || everything || phase1 || ratchet_parts;
do_spool_right        = (option == 0 && make_spool_right)        || (option ==  4)  || everything || phase2;
do_friction_wheel     = (option == 0 && make_friction_wheel)     || (option ==  5)  || everything || phase2;
do_scraper            = (option == 0 && make_scraper);
do_inset              = (option == 0 && make_inset)              || (option ==  6)  || everything || phase2;
do_blocking_spring    = (option == 0 && make_blocking_spring)    || (option ==  7)  || everything || phase2 || ratchet_parts;
do_reel_counterpart   = (option == 0 && make_reel_counterpart)   || (option ==  8)  || everything || phase2;
do_handle_lock        = (option == 0 && make_handle_lock)        || (option ==  9)  || everything || phase2;
do_nozzle_adapter     = (option == 0 && make_nozzle_adapter)     || (option ==  10) || everything;
do_lever_actuator     = (option == 0 && make_lever_actuator)     || (option ==  11) || everything;
do_tape_chute         = (option == 0 && make_tape_chute)         || (option ==  12) || everything || phase2;
do_test_print         = (option == 0 && make_test_print)         || (option ==  13);

debug_ratchet = ratchet_parts;

/* [ Logo and Text ] */

// Switch on/off logos and text (except tag)
logo_enabled=false;
// Logo text to be printed on the reverse of the base plate
logo_text="makr.zone";
// Tag to be printed on the reverse of the base plate (revision number etc.)
logo_tag="";
// Open Source Hardware Logo size (set 0 to switch off)
logo_size=18; 
// Etching depth
logo_etch=0.4; 
// Logo outline pen width
logo_etch_pen=0.8; // [0.2:0.01:2]
// Additional font weight
logo_etch_font=0.2; // [-0.5:0.01:1]
// Logo position in x
logo_x=-60;
// Logo position in y
logo_y=24;
// Text position in x
logo_text_x=-60;
// Text position in x
logo_text_y=10;
// Tag position in x
logo_tag_x=-22;
// Tag position in y
logo_tag_y=-4.5;
// Logo_font 
logo_font="Electrolize:style=Regular"; // ["Electrolize:style=Regular", "Liberation Mono:style=Bold"]
use <Electrolize-Regular.ttf>
// Electrolize-Regular.ttf: Copyright (c) 2011, Cyreal (www.cyreal.org) 
// with Reserved Font Name "Electrolize" This Font Software is licensed 
// under the SIL Open Font License, Version 1.1. This license is available 
// with a FAQ at: http://scripts.sil.org/OFL
// https://github.com/google/fonts/tree/master/ofl/electrolize

// Text font size
logo_font_size=5.4;
logo_tag_font=logo_font;
// Tag font size
logo_tag_font_size=4.6;

/* [ Display ] */

// Arrange the parts as assembled
debug=true;
// Relax the springs in assembled mode
relax_springs=false;
// Render some complex bodies in preview (better quality, slower rendering)
preview_rendering=false;
// Litefeeder reference (from: https://github.com/dining-philosopher/litefeeder)
do_litefeeder=false;

// opacity of main items. 0.7 is a good option. 1.0 is fully opaque.
opacity = 1.0;
// opacity of ancilliary items. 0.2 is a good option. 1.0 is fully opaque.
opacity_low = 1.0;

/*  [ 3D Printing ] */

// Standard layer height
layer_height=0.1;
// Standard extrusion width
extrusion_width=0.4; // [ 0.1 : 0.01 : 1.0 ]
// Minimum gap between parts on the the print bed
gap=2;
// Maximum spacing between supports (0 to switch off)
support_grid=0;

// General play rationale: 
// the play is modelled on the smaller, removable part, so you can tune it with quick re-prints.

// Play between parts that need to snap-in (empirical)
play=-0.02;
// Play on axles (empirical)
axle_play=0.1;

// Play on the spool axle 
spool_axle_play=axle_play;
// Specific snap-in play for inset 
inset_play=play;
// Play on the handle lock
handle_lock_play=play;
// Play on fixtures
fixture_play=play; 

// Minimal sturdy vertical wall 
wall_strength_min=1.3;
// Round up to nearest multiple of extrusion width
wall=ceil(wall_strength_min/extrusion_width)*extrusion_width;
// Minimal sturdy horizontal wall 
layered_wall_strength_min=0.7;
// Round up to nearest multiple of layer height
layer_wall=ceil(layered_wall_strength_min/layer_height)*layer_height;
// bevel/rounding in X/Y
bevel_xy=wall;
// bevel size, in multiples of 1 layer
bevel_multiplier=2;
// bevel in Z
bevel_z=bevel_multiplier*layer_height;

// Maximum allowed error in (most) curve approximations
_fp=0.001; // $fn is determined by this maximum error
// Epsilon for CSG body overlap
e=0.02;
$fs=extrusion_width;


/* [ Tape Specification ] */

// Tape width
tape_width=8; // [8:4:24]
tape_width_8 = 8+0;
// Tape width adjustment for inset.
tape_width_adjust=0.15; // [-0.25:0.01:0.25]
tape_width_eff=tape_width+tape_width_adjust;
// Tape thickness (not incuding the embossed pockets)
tape_thickness=0.6; // [0:0.01:1.5]
// Embossed pockets portruding from the underside of the tape
tape_emboss=0.0; // [0:0.01:12]
    // 250V cap = 1.6
// Embossed pockets size, across tape, measured outside (underside of tape)
tape_emboss_size=3.75; 

// A good place to put a hole in the inset
tape_halfway_hole = 8/2+1.2;

/* [ Tape Specification, Advanced ] */

// Maximum overall tape height for exchangeable insets (should not change)
tape_max_height=4;
// Maximum delta from tape width to reel width (from EIA 481, do not change)
tape_reel_max_width_delta=6.4; 
// Sprocket hole diameter (should not change)
sprocket_hole_diameter=1.5;
// Sprocket hole distance from tape edge (should not change)
sprocket_hole_distance=1.75;
sprocket_hole_margin=sprocket_hole_distance-sprocket_hole_diameter/2;
// Sprocket hole pitch (should not change)
sprocket_pitch=4; 
// maximum sprocket side gap to cover tape
sprocket_gap=sprocket_hole_distance+sprocket_hole_diameter/2;  
// Minimum margin where cover tape is attached
tape_min_margin=0.6; 
sprocket_margin=sprocket_gap+tape_min_margin;

/* [ Tape Inset ] */
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

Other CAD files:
printme/spool-right/spool-right-24mm-161.stl
printme/base/base-16mm-166.stl
printme/inset-paper/left/inset-8mm-left-171.stl
printme/inset-paper/right/inset-8mm-right-scraper-174.stl
printme/base/base-12mm-166.stl
printme/base/base-24mm-extra-deep-166.stl
printme/inset-plastic-extra-deep/right/inset-24mm-extra-deep-right-141.stl
printme/inset-plastic-normal-depth/right/inset-12mm-plastic-right-141.stl
printme/inset-plastic-normal-depth/right/inset-12mm-plastic-right-scraper-141.stl
printme/inset-plastic-normal-depth/right/inset-16mm-plastic-right-141.stl
printme/inset-plastic-normal-depth/right/inset-8mm-plastic-right-171.stl
printme/lever/lever-extra-deep-176.stl
printme/scraper/scraper-12mm-62.stl
printme/spool-drum/drum-16mm-54.stl
printme/spool-drum/drum-24mm-36.stl
printme/spool-drum/drum-8mm-9.stl
printme/spool-friction-wheel/friction-16mm-176.stl
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

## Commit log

2024-08-10 added bevel control option. added fillets to levers
    [PushPullFeeder.scad]
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2024-08-11 avoid bevel undercut
    [PushPullFeeder.scad]
2024-08-11 bearing off by default
    [PushPullFeeder.scad]
2024-08-12 Revert "bevel angle"
    This reverts commit 8630e659c1a75bc3809ab5d154a8f6596479ca0f.
    [PushPullFeeder.scad]
2024-08-12 keep-it-in should not be affected by bevel configuration
    [PushPullFeeder.scad]
2025-01-19 match cura profile (1). play determined by nuts (7)
    [PushPullFeeder.scad]
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2025-01-19 disable reel and extrusion mount. fillet change. break out spool right parts
    [PushPullFeeder.scad]
2025-01-20 Remove engraving. increase axle play to 0.2. allow tape emboss to be deeper. added lumen extrusion mount. added option to enable/disable nozzle tips. added x/y fillet and remove z bevel from friction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
    [PushPullFeeder.scad]
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2025-01-21 smaller fingers on the lumen extrusion mount
    [PushPullFeeder.scad]
2025-01-22 even flat paper has a small embossed backing
    [PushPullFeeder.scad]
2025-01-22 a better lumen mount
    [PushPullFeeder.scad]
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2025-01-22 height fix
    [PushPullFeeder.scad]
2025-01-22 a different way of handling wider tapes
    [PushPullFeeder.scad]
2025-01-22 countersink fix
    [PushPullFeeder.scad]
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2025-01-22 hold the deflector upright
    [PushPullFeeder.scad]
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2025-01-24 revert change adding second thorn
    [PushPullFeeder.scad]
2025-01-24 screw heads are larger
    [PushPullFeeder.scad]
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2025-01-26 two-part inset for wide deep trench
    [PushPullFeeder.scad]
2025-01-26 allow a deeper trench
    [PushPullFeeder.scad]
2025-01-26 the top of the inset is a a long cantilever feature. Add some strain relief on wide feeders that are particularly vulnerable
    [PushPullFeeder.scad]
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2025-01-27 fillet fixes
    [PushPullFeeder.scad]
2025-01-28 thorn fixes
    [PushPullFeeder.scad]
2025-01-28 fix lever width
    [PushPullFeeder.scad]
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2025-02-21 fix lumen mount height
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2025-03-26 short lever is even shorter
    [lever-24mm-53.stl, lever-24mm-60.stl]
2025-03-30 added the 'part scraper' for tapes where the part sticks to the film when peeling
    [PushPullFeeder.scad, inset-12mm-deep-right-scraper-62.stl, inset-8mm-deep-right-scraper-62.stl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]
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2025-04-02 thick paper needs to be more snug too
    [inset-8mm-thick-paper-61.stl, inset-8mm-thick-paper-66.stl, inset-8mm-thick-paper-scraper-62.stl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]
2025-04-02 allow the tape to pass under the dog blocker
    [PushPullFeeder.scad]
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2025-04-11 a different 16mm option. also tighter washer
    [PushPullFeeder.scad, inset-16mm-on-24mm-base-deep-right-70.stl, inset-24mm-deep-left-70.stl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]
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2025-05-21 a lead-in to help insert tape into the slot
    [PushPullFeeder.scad, inset-8mm-deep-right-61.stl, inset-8mm-deep-right-72.stl]
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2025-09-02 fix 'on-ramp' broken during recent model tidy
    [PushPullFeeder.scad]
2025-09-03 add a bumper to prevent the dog striking the top surface of the tape when the dog tooth first engages
    [PushPullFeeder.scad]
2025-09-23 cut back the inset top arm so that it can not jam against any parts which tumble into the sprocket hole
    [PushPullFeeder.scad, inset-12mm-plastic-right-82.stl, inset-12mm-plastic-right-scraper-82.stl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]
2025-09-24 less tight, particularly after the pick window
    [PushPullFeeder.scad]
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2025-10-01 the length of the ratchet levers is a critical parameter for effective film peeling. add a chamfer to defend against any elephants-foot effects
    [PushPullFeeder.scad, blocking-spring-69.stl, blocking-spring-87.stl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]
2025-10-08 sometimes we find the dog does not fully engage with the bumper because of 'elephants foot' expansion on the first layer of the dog where it was in contact with the build plate. This small groove fix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
    [PushPullFeeder.scad, base-8mm-91.stl]
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2025-12-10 1. Change the profile of the "bumper". It now lifts the dog tooth out of one sprocket hole and lowers it into the next. 2. A correspond change to the dog. It is now a cam follower, where the bumper i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
    [PushPullFeeder.scad, base-12mm-111.stl, base-12mm-91.stl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]
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2025-12-12 fix base sizes
    [PushPullFeeder.scad, base-12mm-111.stl, base-12mm-112.stl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]
2026-01-09 a spiral groove allows the slicer to hide the layer start/end point away from the bearing surface
    [PushPullFeeder.scad]
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2026-01-09 Widen the part chute. This prevents jumped parts getting jammed between the chute and their pocket.
    [PushPullFeeder.scad]
2026-01-09 Increase axle play.
    This improves printability on the A1, although I dont really understand why
    the original sizing made the axle tight. Caliper measurements suggest there
    is clearance between the axle and its bearing surface. It does not hurt
    prints on the ultimaker 3.
    [PushPullFeeder.scad]
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2026-01-09 the groove needs to be larger to capture the layer start with Cura's sharpest corner mode
    [PushPullFeeder.scad, base-12mm-119.stl, base-12mm-126.stl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]
2026-01-11 extra deep teeth on the spool ratchet to help assembly
    [PushPullFeeder.scad, spool-left-126.stl, spool-left-35.stl]
2026-01-11 this dog tooth groove needs to be a little wider at the end of the forward stroke, where the dog jumps left onto the ramp
    [PushPullFeeder.scad, inset-24mm-extra-deep-left-127.stl, inset-24mm-extra-deep-left-70.stl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]
2026-01-28 tilt the lever towards the bumper. remove more stress concentrations from the lever
    [PushPullFeeder.scad]
2026-02-06 a new compliant inset for paper tape of all thickness
    [PushPullFeeder.scad, inset-8mm-left-132.stl, inset-8mm-right-132.stl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]
2026-02-08 more friction on the friction wheel. some tweaks to the compliant mechanism too
    [PushPullFeeder.scad]
2026-02-10 plastic tape can use the compliant inset too
    [PushPullFeeder.scad]
2026-02-11 customiser fixes
    [PushPullFeeder.scad]
2026-02-11 tweak the lever. a little less tension pulling to the left, and a tapered profile to avoid stress concentrations. this is still not perfect. The tapered profile does not work with cura slicer, so I a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
    [PushPullFeeder.scad]
2026-02-11 new lever and compliant plastic tape. paper tape has zero top tension
    [inset-24mm-extra-deep-left-141.stl, inset-24mm-extra-deep-left-143.stl, inset-8mm-12mm-16mm-plastic-left-127.stl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]
2026-02-12 add a lump behind the dog window to control tape z. tweak the dog spring, again. We want to use continuous extrusions for the length of the spring, but we also want it wider at the base to match bend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
    [base-12mm-140.stl, base-12mm-146.stl, base-16mm-140.stl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]
2026-02-20 resurrect the clip-on extrusion mount. I'm not sure whether this is better.
    [PushPullFeeder.scad]
2026-02-23 This is a very good solution for the lever. It gets printed with 4 wall extrusions, by setting a thinner wall in the slicer
    [PushPullFeeder.scad, lever-8mm-12mm-16mm-149.stl, lever-8mm-12mm-16mm-152.stl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]
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2026-03-06 Extra friction on the film peeler for 12mm+
    [PushPullFeeder.scad, friction-12mm-161.stl, friction-16mm-161.stl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]
2026-03-15 These two axles are hollow, but the holes dont need to be complete through-holes. Blind holes are better
    [PushPullFeeder.scad]
2026-03-15 an option to have bevels on just one end of an extrusion
    [PushPullFeeder.scad]
2026-03-15 blind hole fix
    [PushPullFeeder.scad]
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2026-03-17 the elephants foot defense on lever axle holes was previously broken when making the axle non-perpendicular
    [PushPullFeeder.scad, lever-8mm-12mm-16mm-152.stl, lever-8mm-12mm-16mm-170.stl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]
2026-03-19 dimension changes following 0402 test. move the inset pick window forward a little; the tape feed position is a little different to previous versions. also provide a slighly tighter grip on the paper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
    [PushPullFeeder.scad, inset-8mm-left-171.stl, inset-8mm-plastic-right-171.stl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]
2026-03-19 Trim off the bottom edge at the level of the top of the inset. This gives a wider tape entry path
    [PushPullFeeder.scad, base-8mm-172.stl]
2026-03-20 move the paper tape inset pick window a little further more, for 0402
    [inset-8mm-left-143.stl, inset-8mm-plastic-right-141.stl, inset-8mm-plastic-right-scraper-141.stl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]
2026-03-24 slightly wider aperture on paper tapes for 0402
    [PushPullFeeder.scad, inset-8mm-right-173.stl, inset-8mm-right-174.stl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]
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2026-05-12 fix for older versions of openscad
    [PushPullFeeder.scad]
